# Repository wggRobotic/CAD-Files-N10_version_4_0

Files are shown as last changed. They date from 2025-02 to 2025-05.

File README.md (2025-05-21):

# Robot components

Here, you will find all the essential components of our N10 robot available as .stp files, allowing anyone to build and customize the robot.

Our robot is a rover equipped with a Rocker-Bogie suspension system, inspired by the Mars rovers and the open-source [Stair Climbing Rover](https://www.printables.com/model/194299-stair-climbing-rover) project by WildWilly. We have modified, enhanced, and completely redesigned various components to meet our specific requirements.

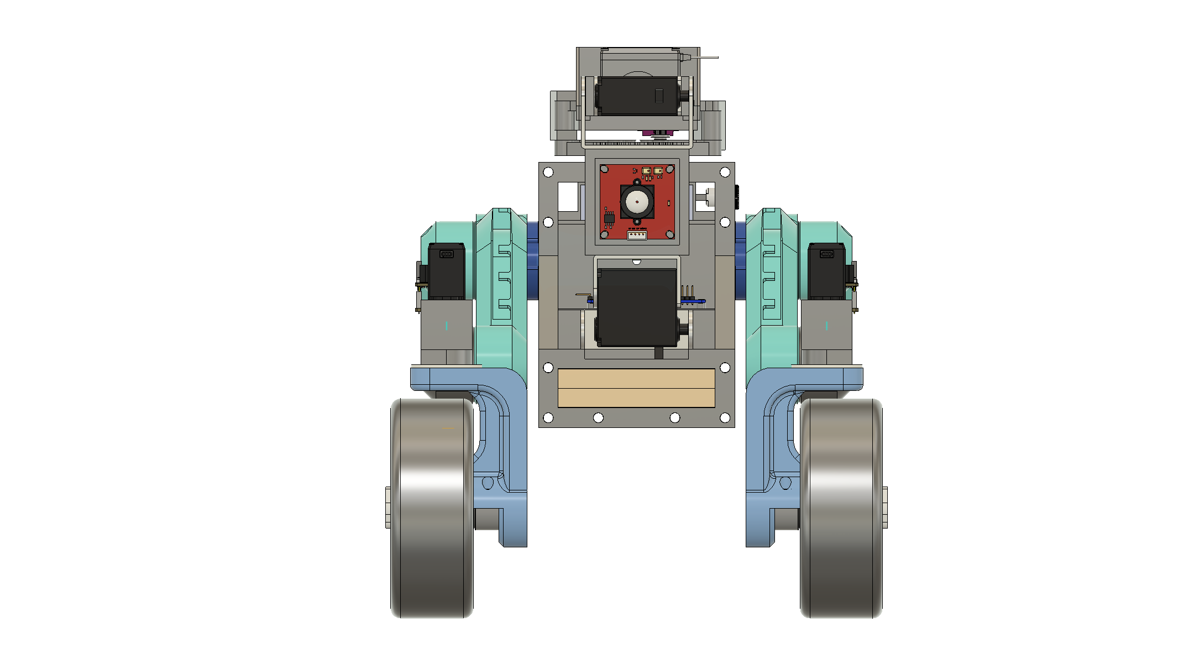
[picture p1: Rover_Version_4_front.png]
N-10_frontview


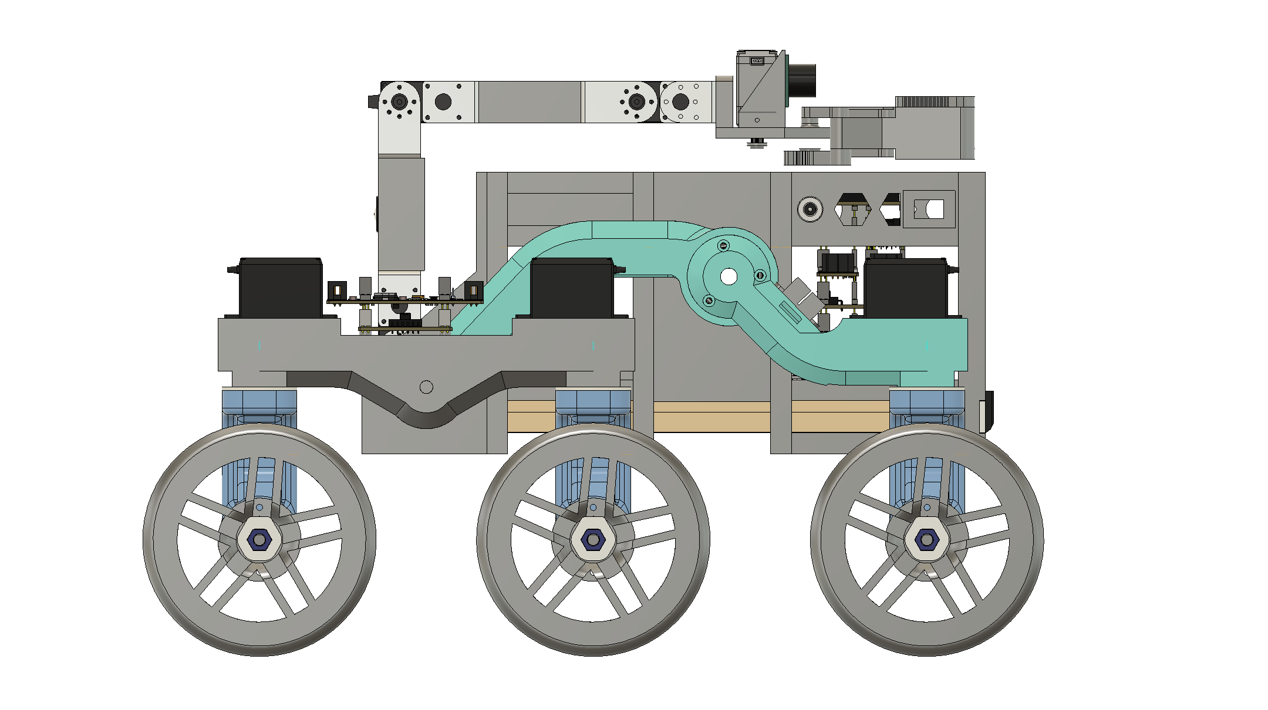
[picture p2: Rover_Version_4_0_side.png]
N-10_sideview


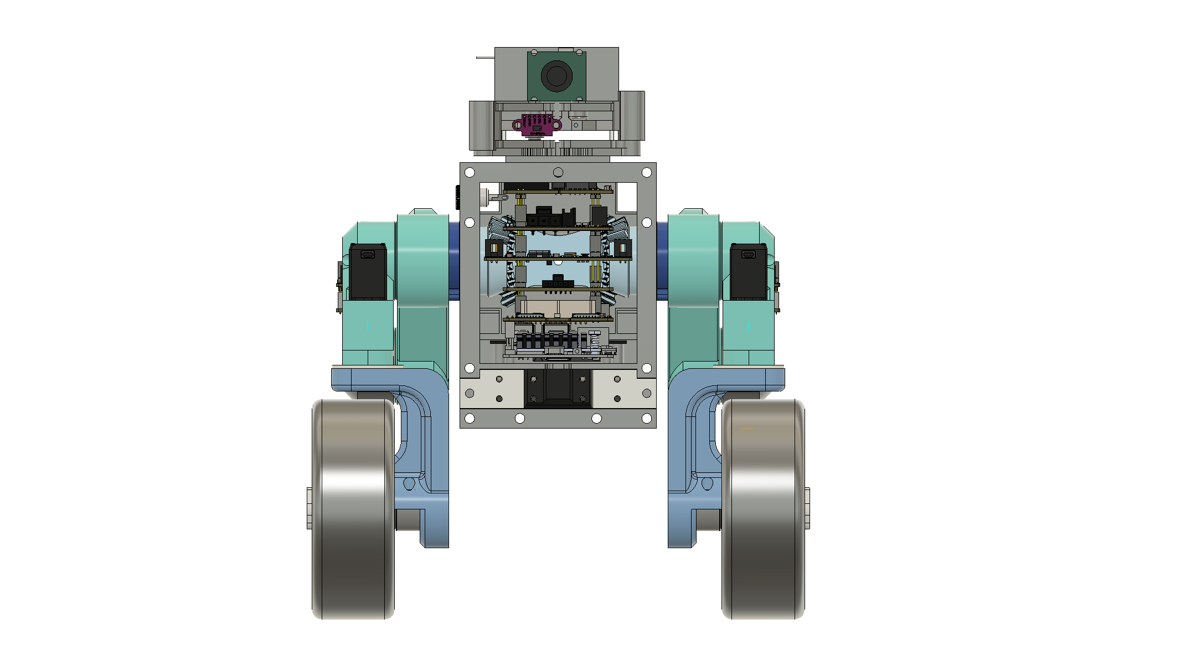
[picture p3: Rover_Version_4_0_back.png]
N-10_back


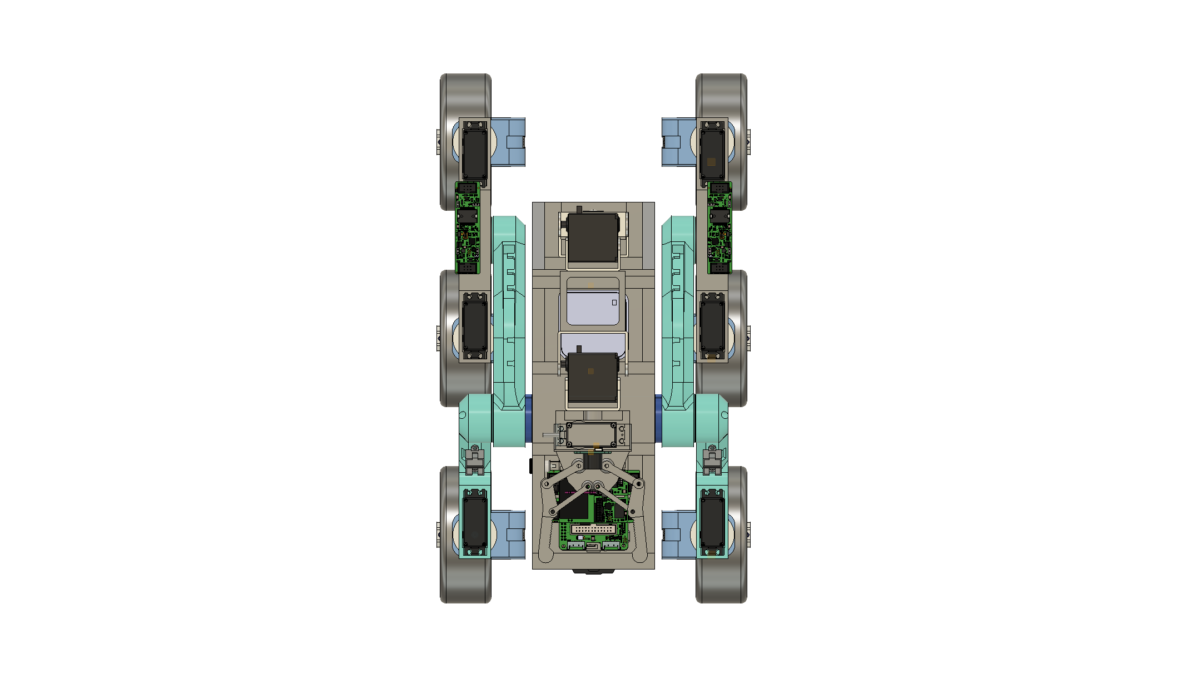
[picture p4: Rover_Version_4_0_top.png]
N-10_top


## Main Body Structure

The main body of the rover is assembled using 3D-printed segments combined with M5 threaded rods. This design ensures a stable, robust, yet lightweight and modular framework. Each segment can be removed individually, making maintenance significantly easier.

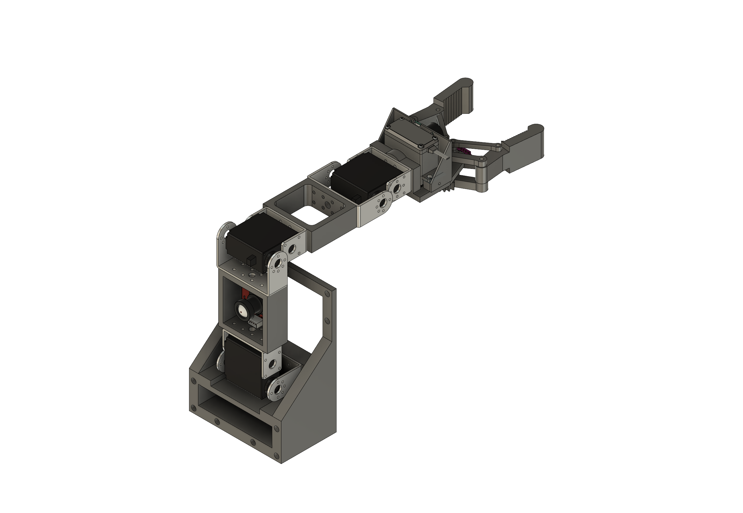
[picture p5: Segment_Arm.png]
Segment_arm


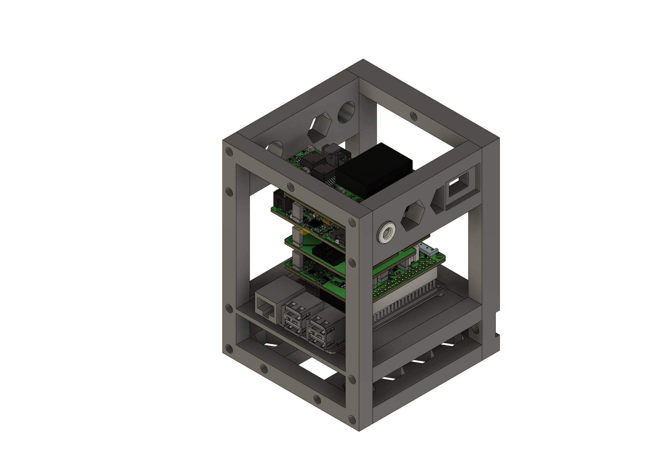
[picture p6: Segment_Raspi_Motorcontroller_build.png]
Segment_raspi


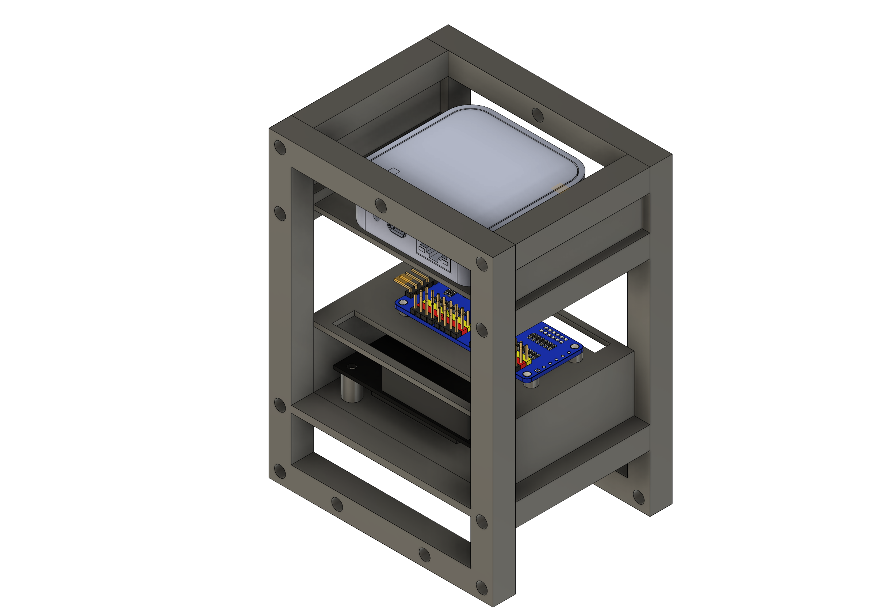
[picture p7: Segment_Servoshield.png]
Segment_shield


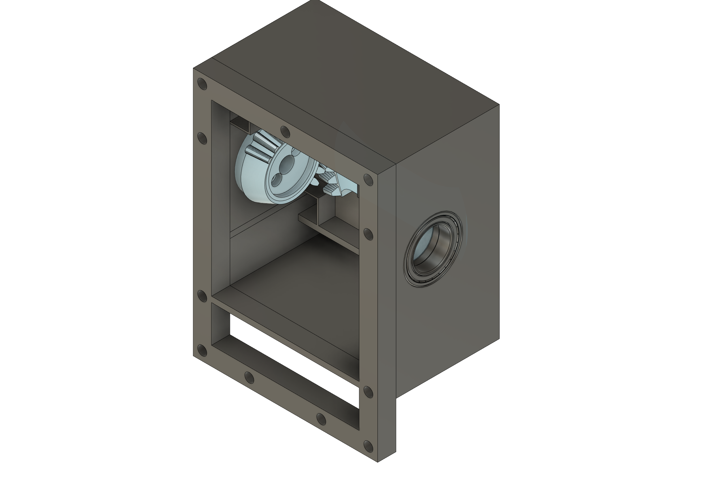
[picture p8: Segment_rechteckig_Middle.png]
Segment_differential


Most of the other components are designed for 3D printing and can be assembled using M3, M2.5, or M2 machine screws. For added stability and support, the servomotors, motor mounts, and wheel hubs are secured within the plastic using [M3 heat-set inserts](https://www.amazon.de/ruthex-Gewindeeinsatz-St%C3%BCck-Gewindebuchsen-Kunststoffteile/dp/B08BCRZZS3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).

In our previous version, the motor attachment parts were a major issue. When printed in PETG, they would break in certain situations and had too much flex. To address this, we redesigned the part for the new version and printed it in nylon using an SLS printer. This was made possible through our collaboration with [Prof. Dr. Koch](https://www.th-nuernberg.de/person/koch-michael/) from the TH Nürnberg.

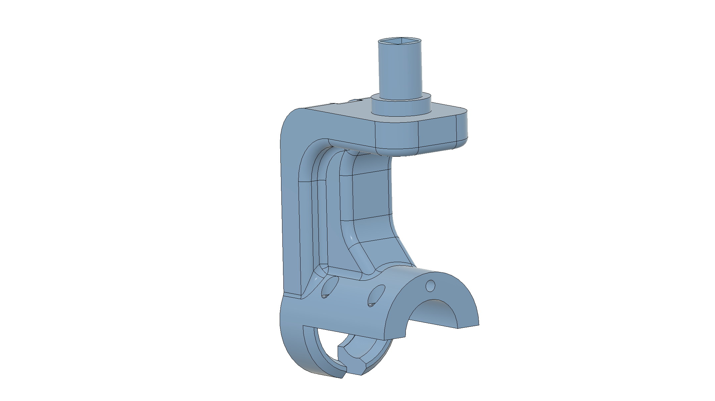
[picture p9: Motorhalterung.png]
Motorhalterung


All other parts can be printed in PETG.

Enjoy building and customizing your own robot!

## Wheel Control and Alignment

The control and alignment of each wheel are managed by Hobby servomotors of the type [MG996](https://www.amazon.de/AZDelivery-Digital-Getriebe-Hubchrauber-Flugzeug/dp/B07H89JH74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). These servomotors are addressed via I2C through an Adafruit PCA9685 servo board.

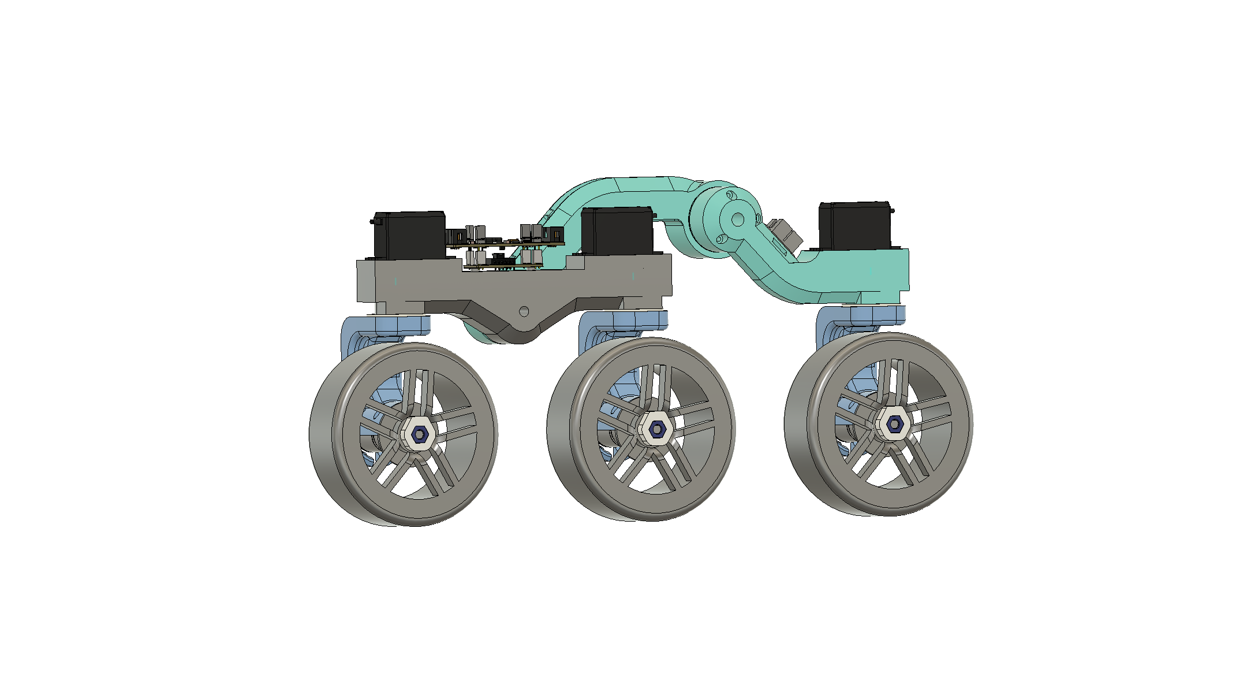
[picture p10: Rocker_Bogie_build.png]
Rocker-Bogie-Suspension


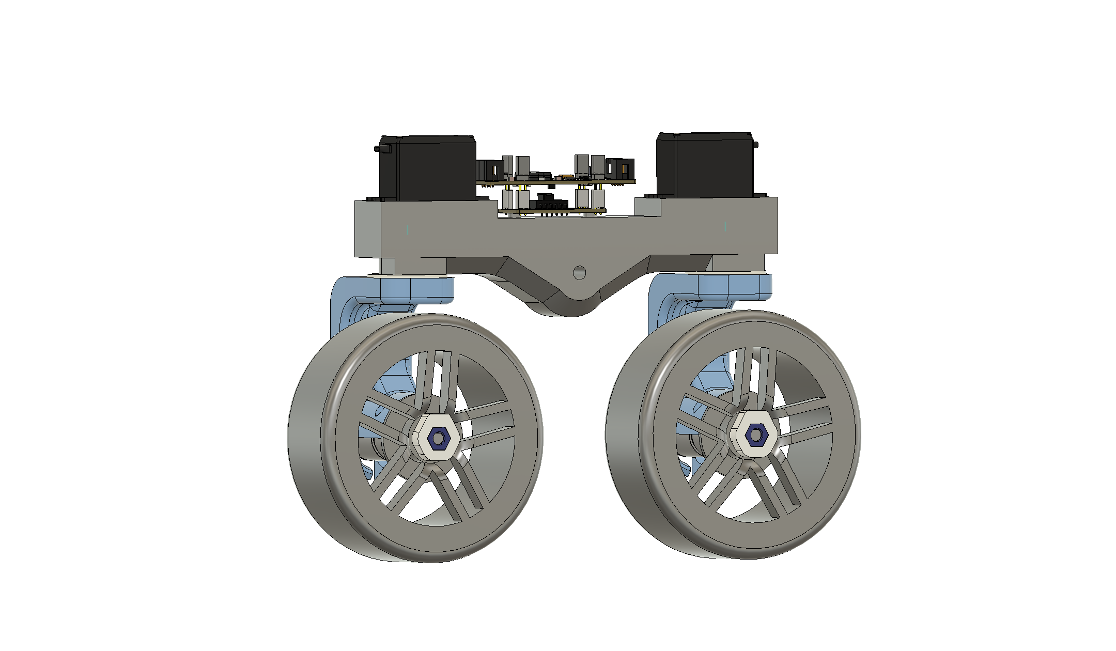
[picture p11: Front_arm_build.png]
Rocker


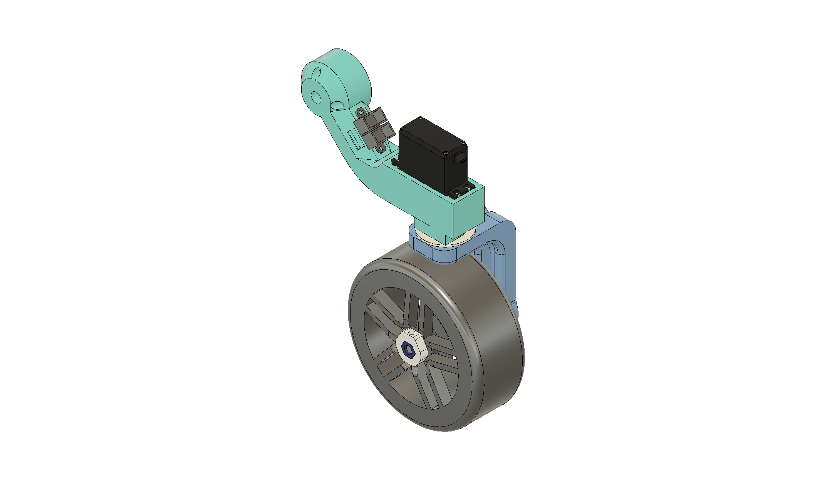
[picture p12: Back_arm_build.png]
Back-arm


The wheel and motor mounts, as well as the wheel hubs, are specially designed for our needs and printed in nylon using an SLS printer. Due to space constraints, the motor mounts had to be fabricated from steel to prevent rotation, as a 2mm-thick printed part would not provide sufficient strength. We are very grateful to [ZF](https://www.zf.com/mobile/de/homepage/homepage.html) in Nuremberg for their support in this process.

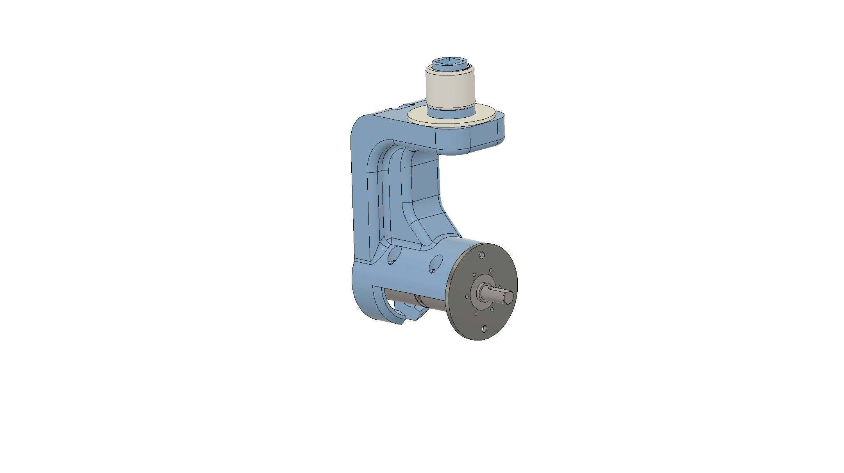
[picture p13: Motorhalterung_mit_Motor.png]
Halterung
)

## Motors and motorcontrol
Our six wheels are powered by Faulhaber DC motors with planetary gearboxes [2224U018S R IEH2-512 22GPT 44:1](https://www.faulhaber.com/de/produkte/serie/22gpt/), generously provided by Faulhaber for this project. Motor control and regulation, as well as the power supply for other components, are handled by a Kinematics Kit, kindly provided by [EduArt Robotik](https://www.eduart-robotik.com/). This kit is designed to be mounted on a Raspberry Pi 4 or [5](https://www.berrybase.de/raspberry-pi-5-8gb-ram) and can be expanded modularly. The basic components of the kit include:

+ Adapter Board either directly pluggable onto a Raspberry Pi 4/5 or as a standalone EduArt Ethernet controller board, with which you can connect any computer with an Ethernet interface. This gives you the freedom to build the computing power into your robot that you need for your desired application. This board is supplied via the socket strips, i.e. a circuit board with the appropriate sockets for a power supply unit or a battery should be used. The possible input voltage Vin is 12V to 55V. Depending on how many motors are connected, the power supply must be able to supply higher currents. High-current batteries are recommended for operating a robot (min. 8A).

+ Motorcontrollers can be plugged in directly. This allows you to control the speed of 1 to 8 motors. The motor controllers are available in two versions, single-channel or dual-channel. Up to four motor controllers can be used, i.e. it is possible to use 1 to 4 larger motors (IRMS up to 5A) or 1 to 8 smaller motors (IRMS up to 2.5A). The dielectric strength of the single-channel motor controllers is 55V. The dielectric strength of the dual-channel motor controllers is 35V.

+ The Power Management Module takes over the charge control of a 19.2V NiMH battery pack and also offers an on/off logic. Temperature monitoring of the battery uses an integrated 6.8kOhm NTC. Never connect a battery other than the one supplied by EduArt.
    
+ The Auxiliary Power Supply Module provides additional voltage levels with which you can supply additional devices. The permissible operating voltage is between 15V and 36V.

Warning: The Raspberry single-board computer is supplied directly via the socket connectors. Never connect an external power supply for the Raspberry via USB-C.

Free_Kinematics_Kit_1920

Free_Kinematics_Kit_Electrical_Interface_Desc_1920

We also use an additional module to distribute the motor driver board’s connections to the rocker elements.

## Power Supply

The power and voltage supply is provided by a NiMH, 19.2V, 4.5 Ah battery pack. Although Nickel-Metal Hydride batteries are significantly heavier than comparable Li-ion batteries, they have much lower risks of fire and explosion. Additionally, these batteries are more maintenance-friendly, which outweighs the disadvantages for us. For powering the Raspberry Pi 5 and the servomotors, the voltage is stepped down using DC-DC converters, as described in the Motor Control section. Specifically, for powering the servomotors, we use an additional DC-DC converter [UWS-5/10-Q12P-C](https://www.digikey.de/de/products/detail/murata-power-solutions-inc/UWS-5-10-Q12P-C/10427628) on our board that supplies the servos on the PCA9685 board with 5V at 10A as an external power source.

## Cameras and Camera Feed

The robot is equipped with two cameras:

+ Front Cameras: Mounted in the first conector element of the robot arm is a [IMX179](https://www.berrybase.de/usb-2.0-hd-kameramodul-8-megapixel-imx179-sensor-1450-mikrofon).
+ Gripper/Rear Camera: A USB camera module [OV2710](https://www.berrybase.de/usb-2.0-kameramodul-2-megapixel-ov2710-sensor-1450-low-light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) is mounted on top of our gripper modul. The camera can also be used as a rearview camera.

All cameras have been recycled from older projects.

In our GUI, users can switch between the different camera feeds with the press of a button.

## Simple Robot Arm Assembly

This section provides a brief description of the simple robot arm mounted on the N10 robot. 

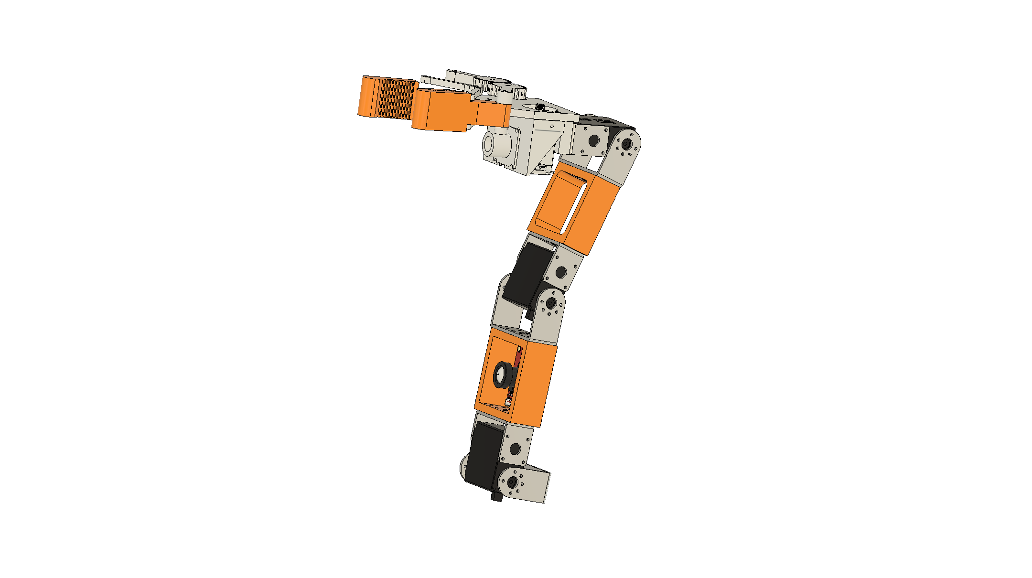
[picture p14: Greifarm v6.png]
Arm_topview


The main components include:

+ Three powerful [Servomotors](https://www.amazon.de/ANNIMOS-Servomotor-Drehmoment-Vollmetallgetriebe-Montagehalterungen/dp/B0C69NNP9P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) with aluminum brackets: These form the basic structure of the arm.
  
+ USB Camera modules [IMX179](https://www.berrybase.de/usb-2.0-hd-kameramodul-8-megapixel-imx179-sensor-1450-mikrofon) and [OV2710](https://www.berrybase.de/usb-2.0-kameramodul-2-megapixel-ov2710-sensor-1450-low-light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)
  
+ Laser distance sensor, build into the gripper: [VL53L0X](https://www.amazon.de/AZDelivery-VL53L0X-Flight-Ranging-Sensor/dp/B086V37JJ7?th=1)
  
+ Gripper: A simple gripper controlled by a Hobby servomotors of the type [MG996](https://www.amazon.de/AZDelivery-Digital-Getriebe-Hubchrauber-Flugzeug/dp/B07H89JH74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).
  
+ Control: The arm is controlled via I2C using an [Adafruit PCA9685 servo board](https://www.amazon.de/PCA9685-16-Kanal-12-Bit-Arduino-Robort/dp/B07Y9PTY12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).
  
+ 3D printed segements between the servos.

## Component-list

Component | Unit price | Quantity | Total price | Note
-------- | :--------: | :--------: | :--------: | --------
MG996 - Servomotor   | 6.00 €   | 7 | 42.00 €   | [Amazon](https://www.amazon.de/AZDelivery-Digital-Getriebe-Hubchrauber-Flugzeug/dp/B07H89JH74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)
ANNIMOS 25kg Servomotor   | 21.9 €   | 3 | 65,97 €   | [Amazon](https://www.amazon.de/ANNIMOS-Servomotor-Drehmoment-Vollmetallgetriebe-Montagehalterungen/dp/B0C69NNP9P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)
EduArt Kinematics Kit  | 786.75 €   | 1 | 786.75 €  | [Eduart Robotik](https://www.eduart-robotik.com/)
Faulhaber DC motors with planetary gearboxes  | 209.20 €   | 6 | 1255.20 €   | [2224U018S R IEH2-512 22GPT 44:1](https://www.faulhaber.com/de/produkte/serie/22gpt/)
Raspberry Pi 5 8Gb  | 86.50 €   | 1 | 86.50 €   | [berrybase](https://www.berrybase.de/raspberry-pi-5-8gb-ram) 
VL53L0X | 7.49 € | 1 | 7.49 € | [Amazon](https://www.amazon.de/AZDelivery-VL53L0X-Flight-Ranging-Sensor/dp/B086V37JJ7?th=1)
USB camera module IMX179 | 49.90 € | 1 | 49.90 € | [berrybase](https://www.berrybase.de/usb-2.0-hd-kameramodul-8-megapixel-imx179-sensor-1450-mikrofon)
USB camera module OV2710 | 33.40 € | 1 | 33.40 € | [berrybase](https://www.berrybase.de/usb-2.0-kameramodul-2-megapixel-ov2710-sensor-1450-low-light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)
PCA9685 Servomotor Drive Module | 6.50 € | 1 | 6.50 € | [Amazon](https://www.amazon.de/PCA9685-16-Kanal-12-Bit-Arduino-Robort/dp/B07Y9PTY12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)
Bambu PETG Filament 1 kg  | 16.99 € | 4 | 67.96 € | [Bambu](https://eu.store.bambulab.com/de/products/petg-hf?variant=49068714623324)
Maschine screws (M2, M2.5 M3) | 24.65 € | 1 | 24.65 € | [Amazon](https://www.amazon.de/Edelstahl-Sechskopf-Knopf-Schrauben-Unterlegscheiben-Sortiment-Aufbewahrung/dp/B07FPGNTXD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)
Heat-Set Inserts | 8.99 € | 1 | 8.99 € | [Amazon](https://www.amazon.de/ruthex-Gewindeeinsatz-St%C3%BCck-Gewindebuchsen-Kunststoffteile/dp/B08BCRZZS3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)
|  | |**TOTAL:** | 2436.31 € |

The total price of all components is very high, but most of the components are high-quality products that can usually be replaced very easily with comparable, significantly cheaper components. For example, simpler [Pololu motors](https://www.pololu.com/category/272/24v-37d-metal-gearmotors) can be used instead of Faulhaber motors. It should also be mentioned at this point that some of these components, were already available from previous projects at our school and have now found a new use. We would also like to thank Faulhaber, EduArt Robotik and Siemens for making their components available to us free of charge.

## Software Control
For more details on software control, please refer to the software section.

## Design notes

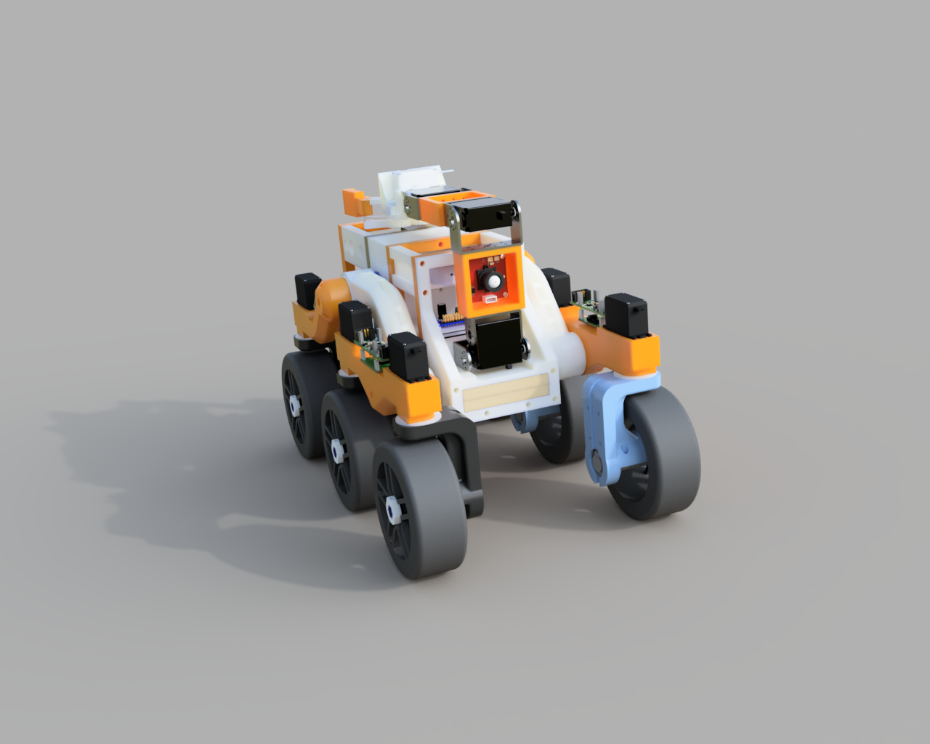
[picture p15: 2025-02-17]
Rover_Render.png

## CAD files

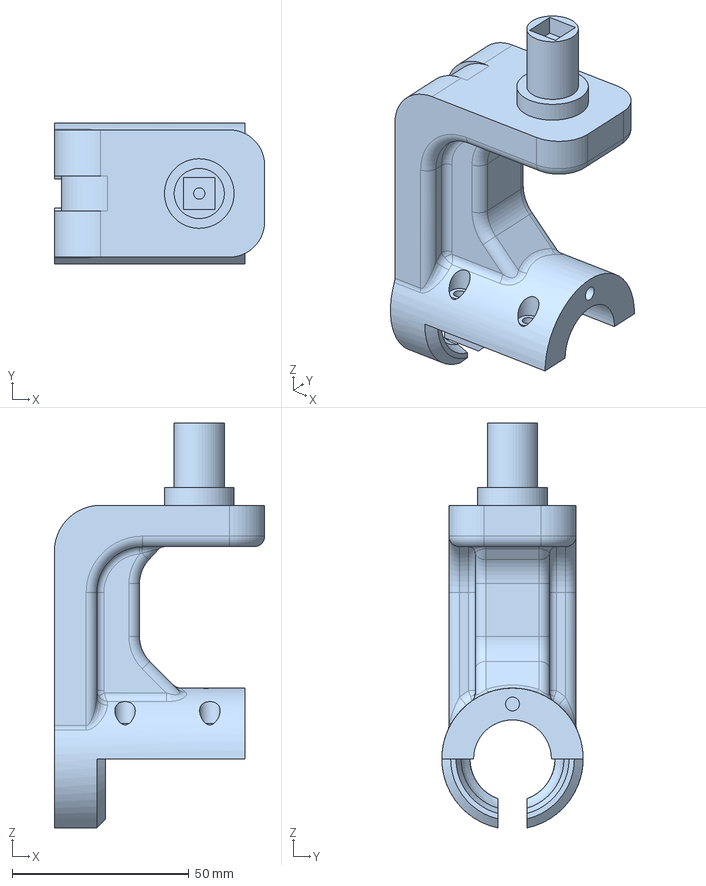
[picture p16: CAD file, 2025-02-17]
Motorhalterung.step
59.5 x 40.0 x 114.6 mm

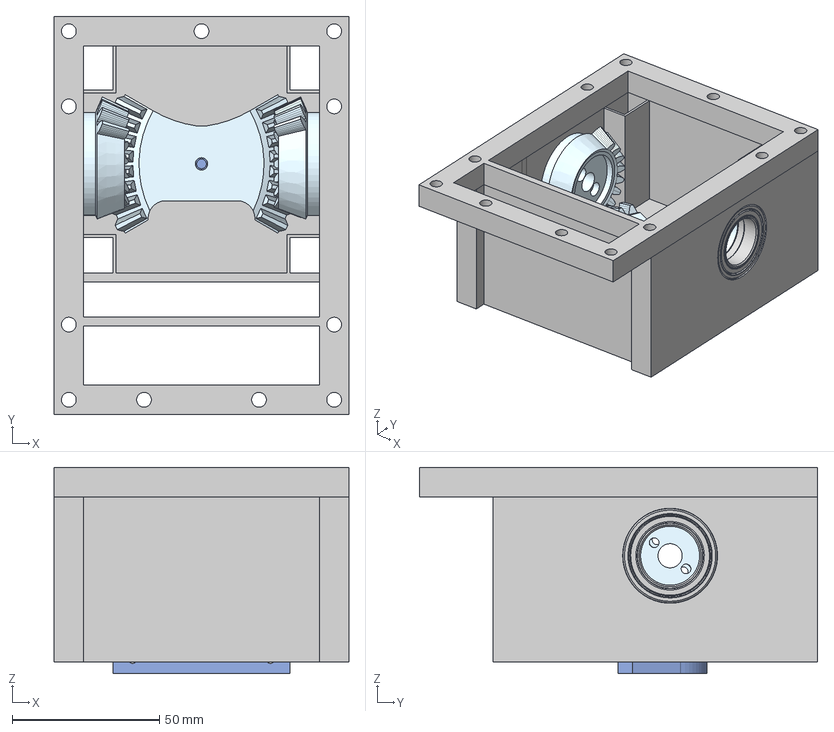
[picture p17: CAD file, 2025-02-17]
Segment_rechteckig_Middle.step
100.0 x 135.0 x 70.0 mm
5972K157_Ball Bearing x 2
Komponente3 x 2
Large_bevel_gear_neu
Segment_rechteckig

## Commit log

2025-02-17 added CAD files
    [Segment_rechteckig_Middle.step]
2025-02-17 added pictures and step filed
    [Motorhalterung.step]
